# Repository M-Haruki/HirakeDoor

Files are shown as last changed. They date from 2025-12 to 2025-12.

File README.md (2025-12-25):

# ひらけドア (HirakeDoor)

教室ドアの自動化プロジェクト  
[PV映像(YouTube)](https://youtu.be/fkIhEhKD6Qc)

## 概要

教室にある横開きの扉を、センサーやモーターなどを用いて、自動ドア化するプロジェクト。  
距離センサーで人の接近を検知し、ステッピングモーターで扉を開閉する。  
閉じる際はおもりによる重力を利用することで、挟まれ事故などを防止している。  
Webインターフェースを用いて、BluetoothLowEnergy(BLE)経由で、手動による扉の開閉を行うこともできる。(BLEに対応するブラウザが必要)

### 背景

冬の教室で扉すぐ横の席は、扉を開きっぱなしにされると非常に寒い。  
だからといって毎回自分で閉めたり、閉めるようお願いするのも手間がかかる。  
そこでこのプロジェクトが始まった。  
第一段階として、扉におもりを取り付け、開けたら勝手に閉まるようなドアクローザー機構を作成。  
概ね好評だったものの、開けるのが重くなるなどの問題もあり、第二段階としてセンサーやモーターなどを用いた自動ドア化を行った。

### 安全対策

扉を閉じる力はおもりの重力のみを使うことで、挟まれた際のリスクを低減し、扉を手動でも開けられるようにした。

## ギャラリー

||||
|:--:|:--:|:--:|
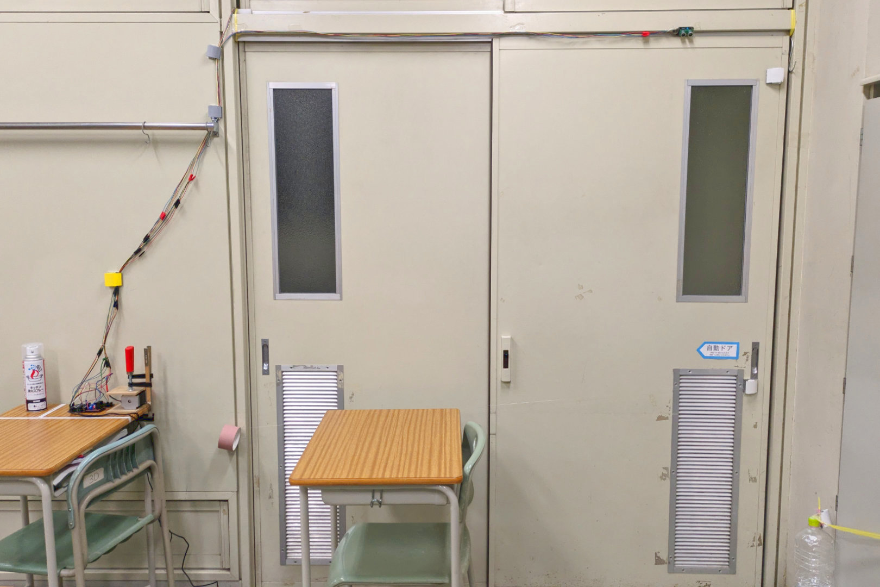
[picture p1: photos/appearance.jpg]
appearance
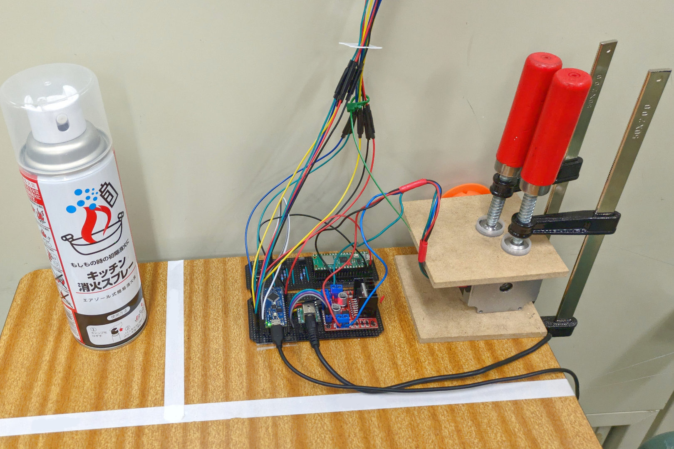
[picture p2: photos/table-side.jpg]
table-side
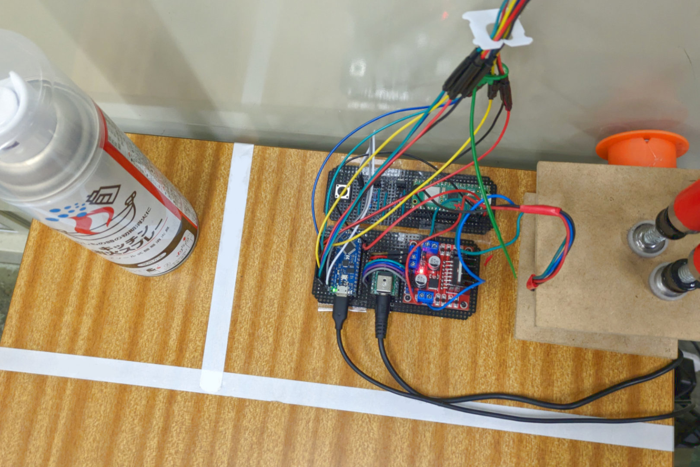
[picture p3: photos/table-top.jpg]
table-top
||||
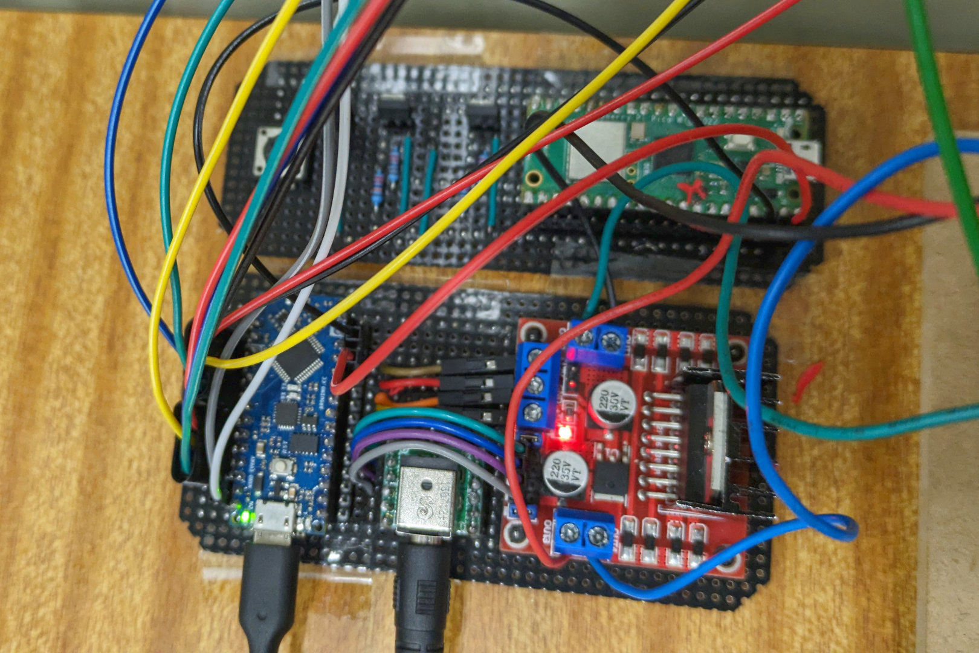
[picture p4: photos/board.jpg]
board
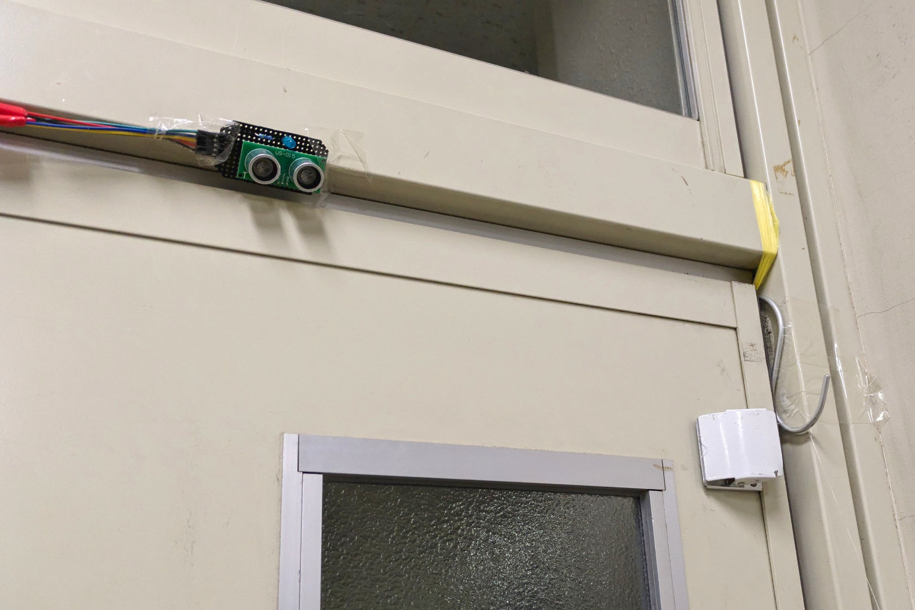
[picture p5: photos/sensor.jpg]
sensor
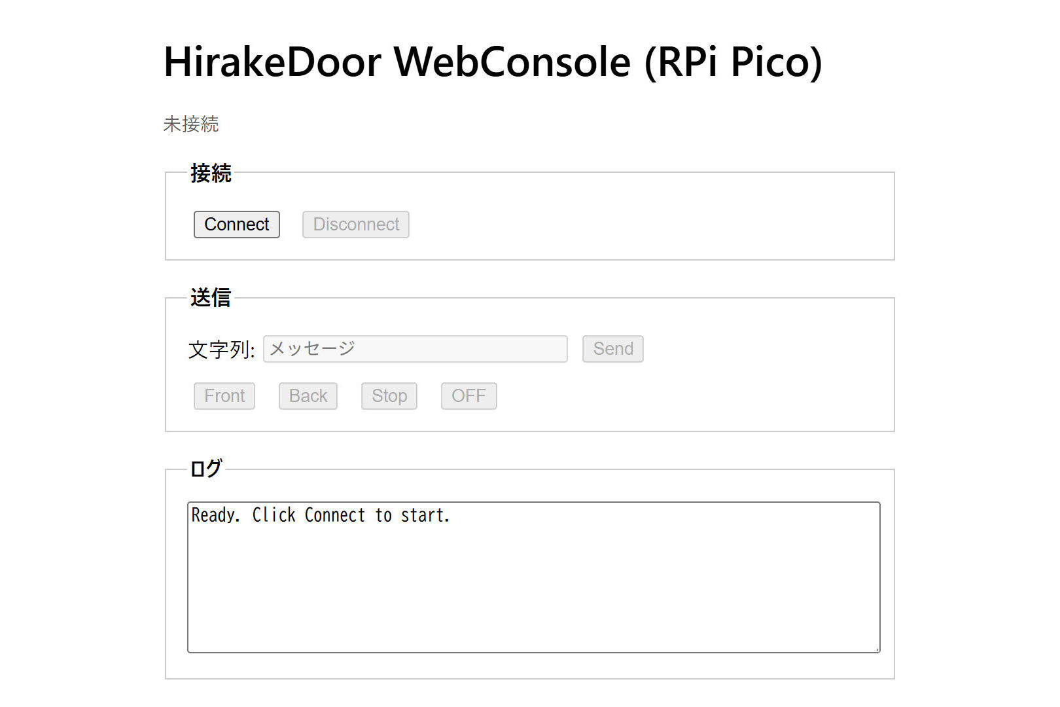
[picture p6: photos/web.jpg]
web
||||

## ソフトウェア構成

- [C++ (Arduino Nano Every)](software/arduino/hirake_door.ino)
- [MicroPython (Raspberry Pi Pico)](software/RPiPico/main.py)
- [HTML (Webインターフェース)](software/web/HirakeDoor.html)

## ハードウェア構成

### 概略図

概略図

### 主要パーツ

- マイコン
  - Arduino Nano Every
  - Raspberry Pi Pico
- ステッピングモーター
  - ST-57BYG076
- モータードライバー
  - L298N モジュール
- 超音波距離センサー
  - US-015

詳細は[hardware/parts.csv](hardware/parts.csv)を参照。

### 回路図

回路図

## クレジット

### プロジェクトメンバー

- M_Haruki
- bearkou
- mochi_kumo
- Mr.Chi

### Special Thanks

- 3D(78th)

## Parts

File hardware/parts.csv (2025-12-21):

Reference | Qty | Value
A1 | 1 | Arduino_Nano_Every
A2 | 1 | RaspberryPi_Pico_W
D1,D2 | 2 | LED
J1 | 1 | Jack-DC
M1 | 1 | ST-57BYG076
Q1,Q2 | 2 | 2SK4017
R1,R2 | 2 | 470Ω
R3,R5 | 2 | 220kΩ
R4,R6 | 2 | 2.2kΩ
SW1 | 1 | SW_Push
U1,U2 | 2 | US-015
U3 | 1 | L298N_Module

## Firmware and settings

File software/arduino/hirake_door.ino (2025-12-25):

// ## 設定構造体とクラス定義
struct SteppingMotorConf
{
  int pinA1;
  int pinA2;
  int pinB1;
  int pinB2;
  float doorPositionLimit;
  float frontStep;
  float backStep;
};

class SteppingMotor
{
private:
  int count = 3; // 0~3
  int pinA1;
  int pinA2;
  int pinB1;
  int pinB2;
  float doorPosition = 0;
  float doorPositionLimit;
  float frontStep;
  float backStep;

  void io(int pin1, int pin2, int state)
  {
    switch (state)
    {
    case -1:
      digitalWrite(pin1, LOW);
      digitalWrite(pin2, HIGH);
      break;
    case 1:
      digitalWrite(pin1, HIGH);
      digitalWrite(pin2, LOW);
      break;
    default:
      digitalWrite(pin1, LOW);
      digitalWrite(pin2, LOW);
      break;
    }
  }

  void move(int a, int b)
  { // -1 or 0 or 1
    io(pinA1, pinA2, a);
    io(pinB1, pinB2, b);
  }

public:
  enum Direction
  {
    Front,
    Back,
  };

  SteppingMotor(const SteppingMotorConf &conf)
  {
    pinA1 = conf.pinA1;
    pinA2 = conf.pinA2;
    pinB1 = conf.pinB1;
    pinB2 = conf.pinB2;
    pinMode(pinA1, OUTPUT);
    pinMode(pinA2, OUTPUT);
    pinMode(pinB1, OUTPUT);
    pinMode(pinB2, OUTPUT);
    doorPositionLimit = conf.doorPositionLimit;
    frontStep = conf.frontStep;
    backStep = conf.backStep;
  }

  bool stepWithLimit(SteppingMotor::Direction direction) // スコープ指定がないとコンパイルエラーになる
  {
    // 超過した値を修正
    if (doorPosition > doorPositionLimit)
    {
      doorPosition = doorPositionLimit;
    }
    else if (doorPosition < 0)
    {
      doorPosition = 0;
    }
    // モーター動作と位置を加算
    if (direction == Front && doorPosition < doorPositionLimit)
    {
      step(Front);
      doorPosition += frontStep;
      if (doorPosition >= doorPositionLimit)
      {
        softStop();
        return true;
      }
      else
      {
        return false;
      }
    }
    else if (direction == Back && doorPosition > 0)
    {
      step(Back);
      doorPosition += backStep;
      if (doorPosition <= 0)
      {
        softStop();
        return true;
      }
      else
      {
        return false;
      }
    }
    else
    {
      return false;
    }
  }

  void step(SteppingMotor::Direction direction)
  {
    // count
    if (direction == Front)
    {
      count += 1;
    }
    else
    {
      count -= 1;
    }
    if (count == 4)
    {
      count = 0;
    }
    else if (count == -1)
    {
      count = 3;
    }
    // move
    switch (count)
    {
    case 0:
      move(1, 1);
      break;
    case 1:
      move(1, -1);
      break;
    case 2:
      move(-1, -1);
      break;
    case 3:
      move(-1, 1);
      break;
    }
  }

  void hardStop()
  {
    switch (count)
    {
    case 0:
      move(1, 1);
      break;
    case 1:
      move(1, -1);
      break;
    case 2:
      move(-1, -1);
      break;
    case 3:
      move(-1, 1);
      break;
    }
  }

  void softStop()
  {
    move(0, 0);
  }

  void resetDoorPosition()
  {
    doorPosition = 0;
  }
};

struct DistanceSensorConf
{
  int pinTrig;
  int pinEcho;
  int pinLed;
  int sampleTimes;
  float sampleTolerance;
  unsigned long ledOnDuration_us;
};

class DistanceSensor
{
private:
  int pinTrig;
  int pinEcho;
  int pinLed;

  int triggerCount = 0; // 0,1,2
  unsigned long triggerTime_us = 0;

  unsigned long startTime;
  unsigned long endTime;
  int lastEchoState;

  static const int sampleTimesMax = 20;
  int sampleTimes;
  int sampleCount;
  float samples[sampleTimesMax];
  float result;
  float sampleTolerance; // 外れ値判定用の許容範囲(中央値に対する割合)

  unsigned long ledOnDuration_us; // LED点灯時間(μs)
  unsigned long ledOnTime_us = 0; // LED点灯時間管理用

  enum SensorMode
  {
    WaitStart,
    Trigger,
    Measuring,
    WaitNextMeasure,
    Completed,
  };
  SensorMode sensorMode = WaitStart;

  void startMeasure()
  {
    lastEchoState = LOW;
    triggerCount = 0; // 安全のため
    sensorMode = Trigger;
  }

  void trigger()
  {
    switch (triggerCount)
    {
    case 0:
      digitalWrite(pinTrig, LOW);
      triggerTime_us = micros();
      triggerCount = 1;
      break;
    case 1:
      if (micros() - triggerTime_us >= 2)
      {
        digitalWrite(pinTrig, HIGH);
        triggerTime_us = micros();
        triggerCount = 2;
      }
      break;
    case 2:
      if (micros() - triggerTime_us >= 10)
      {
        digitalWrite(pinTrig, LOW);
        triggerCount = 0;
        sensorMode = Measuring;
      }
    }
  }

  bool captureEcho()
  {
    // 計測完了でtrueを返す
    int state = digitalRead(pinEcho);
    if (lastEchoState == LOW && state == HIGH)
    {
      // LOW → HIGH（立ち上がり）
      startTime = micros();
      lastEchoState = HIGH;
      return false;
    }
    else if (lastEchoState == HIGH && state == LOW)
    {
      // HIGH → LOW（立ち下がり）
      endTime = micros();
      lastEchoState = LOW;
      return true;
    }
    else
    {
      return false;
    }
  }

  float getDistance()
  {
    long duration = endTime - startTime;
    float distance = duration * 0.0343 / 2.0;
    if (distance >= 2 && distance <= 400)
    {
      return distance;
    }
    else
    {
      return -1;
    }
  }

  float filter()
  {
    // 配列のコピーを作ってソート
    float sorted[sampleTimesMax];
    memcpy(sorted, samples, sampleTimes * sizeof(float));
    for (int i = 0; i < sampleTimes - 1; i++)
    {
      for (int j = i + 1; j < sampleTimes; j++)
      {
        if (sorted[i] > sorted[j])
        {
          float tmp = sorted[i];
          sorted[i] = sorted[j];
          sorted[j] = tmp;
        }
      }
    }
    // 中央値
    float median = sorted[sampleTimes / 2];
    // 外れ値除外(中央値 ± 15%)
    float sum = 0;
    int count = 0;
    for (size_t i = 0; i < sampleTimes; i++)
    {
      if (fabs(samples[i] - median) < median * sampleTolerance)
      {
        sum += samples[i];
        count++;
      }
    }
    // 平均値計算
    if (count == 0)
    {
      return -1; // 全て外れ値 → 失敗
    }
    return sum / count;
  }

public:
  DistanceSensor(const DistanceSensorConf &conf)
  {
    pinTrig = conf.pinTrig;
    pinEcho = conf.pinEcho;
    pinLed = conf.pinLed;
    pinMode(pinTrig, OUTPUT);
    pinMode(pinEcho, INPUT);
    pinMode(pinLed, OUTPUT);
    sampleTimes = conf.sampleTimes;
    sampleTolerance = conf.sampleTolerance;
    ledOnDuration_us = conf.ledOnDuration_us;
  }

  void ledOn()
  {
    digitalWrite(pinLed, HIGH);
    ledOnTime_us = micros();
  }

  void clock()
  {
    switch (sensorMode)
    {
    case Trigger:
      trigger();
      break;
    case Measuring:
      bool isEnd = captureEcho();
      if (isEnd)
      {
        samples[sampleCount] = getDistance();
        sensorMode = WaitNextMeasure;
        sampleCount += 1;
        if (sampleCount == sampleTimes)
        {
          // 平均を計算
          result = filter();
          sensorMode = Completed;
        }
        else
        {
          startMeasure();
        }
      }
      break;
    }
    // LED消灯管理
    if (ledOnTime_us != 0 && micros() - ledOnTime_us >= ledOnDuration_us)
    {
      digitalWrite(pinLed, LOW);
      ledOnTime_us = 0;
    }
  }

  void start()
  {
    if (sensorMode == WaitStart)
    {
      sampleCount = 0;
      startMeasure();
    }
  }

  float getResult()
  {
    if (sensorMode == Completed)
    {
      sensorMode = WaitStart;
      return result;
    }
    else
    {
      return -1;
    }
  }
};

struct ManualControlConf
{
  int pinA;
  int pinB;
};
class ManualControl
{
  // プルアップを介すため、LOWがON、HIGHがOFFになる
private:
  int pinA;
  int pinB;

public:
  enum Status
  {
    Front,
    Back,
    Stop,
  };

  ManualControl(const ManualControlConf &conf)
  {
    pinA = conf.pinA;
    pinB = conf.pinB;
    pinMode(pinA, INPUT_PULLUP);
    pinMode(pinB, INPUT_PULLUP);
  }

  bool isManualMode()
  {
    int stateA = digitalRead(pinA);
    int stateB = digitalRead(pinB);
    if (stateA == HIGH && stateB == HIGH)
    {
      return false;
    }
    else
    {
      return true;
    }
  }

  ManualControl::Status status()
  {
    int stateA = digitalRead(pinA);
    int stateB = digitalRead(pinB);
    if (stateA == LOW && stateB == LOW)
    {
      return ManualControl::Stop;
    }
    else if (stateA == LOW && stateB == HIGH)
    {
      return ManualControl::Front;
    }
    else if (stateA == HIGH && stateB == LOW)
    {
      return ManualControl::Back;
    }
  }
};

// ## enum,プロトタイプ宣言(ないとコンパイルエラーになる)
enum MainMode
{
  Close,
  Opening,
  Open,
  Closing,
  Manual,
};
void changeMode(MainMode newMode);

// ## 変数定義(ユーザー変更可能エリア)
SteppingMotorConf motorConf = {
    .pinA1 = 17,
    .pinA2 = 14,
    .pinB1 = 15,
    .pinB2 = 16,
    .doorPositionLimit = 1450, // ドア全開位置の1/4ステップ数
    .frontStep = 1,
    .backStep = -1,
};
DistanceSensorConf distanceAConf = {
    .pinTrig = 2,
    .pinEcho = 3,
    .pinLed = 4,
    .sampleTimes = 10,           // 1度の距離算出のためのセンサー測定回数
    .sampleTolerance = 0.10,     // 外れ値判定用の許容範囲(中央値に対する割合)
    .ledOnDuration_us = 1000000, // LED点灯時間(μs)
};
DistanceSensorConf distanceBConf = {
    .pinTrig = 8,
    .pinEcho = 9,
    .pinLed = 10,
    .sampleTimes = 10,           // 1度の距離算出のためのセンサー測定回数
    .sampleTolerance = 0.10,     // 外れ値判定用の許容範囲(中央値に対する割合)
    .ledOnDuration_us = 1000000, // LED点灯時間(μs)
};
ManualControlConf manualConf = {
    .pinA = 11,
    .pinB = 12,
};
constexpr unsigned long sensorMeasureInterval_us = 50000;       // センサー測定間隔(μs) 小さすぎると測定に失敗しやすい
constexpr unsigned int detectDistanceMin_cm = 5;                // センサー検出距離下限(cm)
constexpr unsigned int detectDistanceMax_cm = 55;               // センサー検出距離上限(cm)
constexpr unsigned long motorStepDurationFront_us = 3750;       // 開く時のモーター1/4ステップ間隔(μs)
constexpr unsigned long motorStepDurationBack_us = 2650;        // 閉じる時のモーター1/4ステップ間隔(μs)
constexpr unsigned long motorStepDurationMaintenance_us = 7000; // メンテナンス時のモーター1/4ステップ間隔(μs)
constexpr unsigned long openCountLimit_ms = 1000;               // ドア全開時間(ms)
bool enableManualMode = true;                                   // マニュアル制御モード有効フラグ

// ## インスタンス生成,グローバル変数定義
SteppingMotor motor(motorConf);
DistanceSensor distanceA(distanceAConf);
DistanceSensor distanceB(distanceBConf);
ManualControl manual(manualConf);
unsigned long lastTrigTime_us = 0;
unsigned long lastStepTime_us = 0;
unsigned long openCount = 0;
MainMode mode = Close;
int usingSensor = 0; // 0:A, 1:B

// ## 関数定義
void changeMode(MainMode newMode)

{
  switch (newMode)
  {
  case Open:
    openCount = openCountLimit_ms;
    break;
  }
  mode = newMode;
  switch (mode)
  {
  case Opening:
    Serial.println("mode:Opening");
    break;
  case Open:
    Serial.println("mode:Open");
    break;
  case Closing:
    Serial.println("mode:Closing");
    break;
  case Close:
    Serial.println("mode:Close");
    break;
  case Manual:
    Serial.println("mode:Manual");
    break;
  }
}

// ## Arduino標準初期処理
void setup()
{
  Serial.begin(9600);
  delay(1000);
  Serial.println("--Initialized--");
  motor.softStop();
}

// ## Arduino標準ループ処理
void loop()
{

  unsigned long now_us = micros();
  distanceA.clock();
  distanceB.clock();
  // 距離センサーによる検出処理
  if (mode == Close || mode == Closing || mode == Open)
  {
    // センサー起動
    if (now_us - lastTrigTime_us >= sensorMeasureInterval_us)
    {
      lastTrigTime_us = now_us;
      switch (usingSensor)
      {
      case 0:
        usingSensor = 1;
        distanceA.start();
        break;
      case 1:
        usingSensor = 0;
        distanceB.start();
        break;
      }
    }
    // 結果取得
    float resultA = distanceA.getResult();
    float resultB = distanceB.getResult();
    float result = (resultA >= 0) ? resultA : resultB;
    // 検出判定
    if (result >= detectDistanceMin_cm && result <= detectDistanceMax_cm)
    {
      if (resultA >= 0)
      {
        distanceA.ledOn();
      }
      else
      {
        distanceB.ledOn();
      }
      Serial.println("distanceDetect:" + String(result));
      if (mode != Open)
      {
        // temp
        if (mode == Closing)
        {
          Serial.println("temp");
          motor.hardStop();
          delay(1200);
          // delayMicroseconds(500000);
        }
        //
        changeMode(Opening);
      }
      else
      {
        openCount = openCountLimit_ms; // open時に時間延長
      }
    }
  }
  // モーター動作
  switch (mode)
  {
  case Opening:
    if (now_us - lastStepTime_us >= motorStepDurationFront_us)
    {
      // 実行頻度が高いため、ここにSerial.println()を入れると距離センサー系の機能がうまく動かない
      lastStepTime_us = now_us;
      bool isEnd = motor.stepWithLimit(SteppingMotor::Front);
      if (isEnd)
      {
        changeMode(Open);
      }
    }
    break;
  case Closing:
    if (now_us - lastStepTime_us >= motorStepDurationBack_us)
    {
      lastStepTime_us = now_us;
      bool isEnd = motor.stepWithLimit(SteppingMotor::Back);
      if (isEnd)
      {
        changeMode(Close);
      }
    }
    break;
  case Open:
    if (now_us - lastStepTime_us >= 1000 && openCount > 0) // 1msごとにトリガー
    {
      lastStepTime_us = now_us;
      openCount -= 1;
      motor.hardStop();
      if (openCount == 0)
      {
        changeMode(Closing);
      }
    }
    break;
  case Manual:
    ManualControl::Status status = manual.status();
    switch (status)
    {
    case ManualControl::Front:
      if (now_us - lastStepTime_us >= motorStepDurationMaintenance_us)
      {
        lastStepTime_us = now_us;
        motor.step(SteppingMotor::Front);
      }
      break;
    case ManualControl::Back:
      if (now_us - lastStepTime_us >= motorStepDurationMaintenance_us)
      {
        lastStepTime_us = now_us;
        motor.step(SteppingMotor::Back);
      }
      break;
    case ManualControl::Stop:
      motor.softStop();
      break;
    }
    break;
  }
  // マニュアル制御確認
  if (enableManualMode)
  {
    if (manual.isManualMode() && mode != Manual)
    {
      changeMode(Manual);
    }
    else if (!manual.isManualMode() && mode == Manual)
    {
      motor.resetDoorPosition();
      changeMode(Close);
    }
  }
}

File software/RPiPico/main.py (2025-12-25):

# BleTest.py
# https://logikara.blog/picow-ble-micropython を参照して作成
# BLEのPeripheralとして振る舞う

import aioble  # MicroPythonのBLEライブラリ
import bluetooth  # MicroPythonのBLEモジュール
import uasyncio as asyncio  # 非同期処理ライブラリ
from machine import Pin  # PicoのGPIOモジュールをインポート

UART_SERVICE_UUID = bluetooth.UUID(
    "6E400001-B5A3-F393-E0A9-E50E24DCCA9E"
)  # UARTサービスUUID
UART_RX_CHAR_UUID = bluetooth.UUID(
    "6E400002-B5A3-F393-E0A9-E50E24DCCA9E"
)  # UART受信用キャラクタリスティックUUID
UART_TX_CHAR_UUID = bluetooth.UUID(
    "6E400003-B5A3-F393-E0A9-E50E24DCCA9E"
)  # UART送信用キャラクタリスティックUUID

# サービスとキャラクタリスティックの定義
uart_service = aioble.Service(UART_SERVICE_UUID)  # UARTサービスを定義
tx_char = aioble.Characteristic(
    uart_service, UART_TX_CHAR_UUID, read=True, notify=True
)  # UART送信用キャラクタリスティックを定義
rx_char = aioble.Characteristic(
    uart_service, UART_RX_CHAR_UUID, write=True, write_no_response=True, capture=True
)  # UART受信用キャラクタリスティックを定義

aioble.register_services(uart_service)  # GATTサービスを登録

led = Pin("LED", Pin.OUT)  # LED端子をledとして出力に設定
out_a = Pin(16, Pin.OUT)
out_b = Pin(17, Pin.OUT)
out_a.value(0)  # 初期状態はOFF
out_b.value(0)
# sw_main = Pin(14, Pin.IN, Pin.PULL_DOWN)  # 送信ボタン
sw_reset = Pin(15, Pin.IN, Pin.PULL_DOWN)  # 接続解除用ボタン


# 非同期でタスクを実行
async def handle_rx(connection):
    # 受信待ちループ
    while connection.is_connected():
        try:
            _, value = await rx_char.written()  # 戻り値のconnectionは未使用
            print("Received:", value)
            v = value.strip().lower()
            if v == b"front":
                out_a.value(1)
                out_b.value(0)
            elif v == b"back":
                out_a.value(0)
                out_b.value(1)
            elif v == b"stop":
                out_a.value(1)
                out_b.value(1)
            elif v == b"off":
                out_a.value(0)
                out_b.value(0)
        except asyncio.CancelledError:
            raise
        except Exception as e:
            print("ReceiveError:", e)
            break


# async def handle_tx(connection):
#     # 送信ループ（変化時のみ通知）
#     last = None
#     while connection.is_connected():
#         try:
#             value = "on" if sw_main.value() else "off"
#             if value != last:
#                 last = value
#                 try:
#                     await tx_char.notify(connection, value.encode())
#                 except asyncio.CancelledError:
#                     raise
#                 except Exception:
#                     # 未購読や一時的な送信失敗はスキップ
#                     pass
#         except asyncio.CancelledError:
#             raise
#         except Exception as e:
#             print("SendError:", e)
#             break
#         await asyncio.sleep_ms(100)


async def handle_disconnect(connection):
    # 接続解除ボタン用ループ
    while connection.is_connected():
        try:
            if sw_reset.value():
                await connection.disconnect()
        except asyncio.CancelledError:
            raise
        except Exception as e:
            print("DisconnectError:", e)
            break
        await asyncio.sleep_ms(100)


# BLE Peripheralとして動作するメインループ
async def ble_peripheral_loop():
    led.value(1)
    await asyncio.sleep_ms(3000)  # 起動後3秒間LED点灯
    led.value(0)
    while True:
        led.value(0)  # 接続待機中はLED消灯
        print("Waiting connect...")
        try:
            async with await aioble.advertise(  # BLEアドバタイズを開始
                250_000,  # アドバタイズ間隔（マイクロ秒）
                name="HirakeDoor_RPiPico",  # アドバタイズ名（BLE接続デバイス名）
                services=[UART_SERVICE_UUID],  # サービスUUIDを指定
            ) as connection:  # 接続待機
                print("Connecting:", connection.device)  # 接続されたデバイス情報を表示
                led.value(1)

                # 受信処理を別タスクで開始
                rx_task = asyncio.create_task(handle_rx(connection))
                # tx_task = asyncio.create_task(handle_tx(connection))
                disconnect_task = asyncio.create_task(handle_disconnect(connection))

                # 接続が切れるまで待機
                while connection.is_connected():
                    await asyncio.sleep_ms(100)

                # 接続解除 → タスクキャンセル
                rx_task.cancel()
                # tx_task.cancel()
                disconnect_task.cancel()
                led.value(0)  # LED消灯
                print("Disconnected")

        except Exception as e:
            print("Advertise:", repr(e))

        await asyncio.sleep_ms(200)


# 実行
try:
    # PicoのBLE Peripheralとして動作開始
    asyncio.run(ble_peripheral_loop())
except KeyboardInterrupt:
    led.value(0)
    out_a.value(0)
    out_b.value(0)
    print("Cleanup done.")

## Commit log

2025-12-14 関連ファイル追加
    [fritzing.fzz]
2025-12-14 SteppingMotorおよびDistanceSensorクラスのプライベートメソッドを整理し、公開メソッドを追加
2025-12-14 マニュアルモードを実装
2025-12-14 回路画像を追加
2025-12-15 センサー2台体制
2025-12-15 測定結果統合ロジック効率化
2025-12-15 初期値更新
2025-12-15 回路データを更新
    [fritzing.fzz]
2025-12-15 回路データを更新(未エクスポート)
    [fritzing.fzz]
2025-12-16 距離センサーの外れ値判定用の許容範囲を追加
2025-12-17 モーター制御ロジックの修正と手動モードの有効化
2025-12-17 回路図を更新
    [fritzing.fzz]
2025-12-18 ステッピングモーターと距離センサーの設定を改善し、LED制御機能を追加
2025-12-18 freeStop()の実行をMotorクラス側に持たせる
2025-12-18 モーター停止メソッドの名称を変更し、コードの可読性を向上させる
2025-12-18 距離センサーのLED制御機能を追加し、changeMode関数の引数を簡素化
2025-12-18 ManualControlの停止メソッドをsoftStopに変更し、モード遷移の処理を改善
2025-12-18 LED制御の初期状態を設定し、BLE周辺機器ループ内での出力ポートの状態をリセット
2025-12-19 ドア位置リセットメソッドを追加し、距離センサーのLED点灯時間を延長、モーターのステップ間隔を調整
2025-12-19 プロジェクト名を「HirakeDoma」から「HirakeDoor」に変更し、関連するファイルのタイトルを更新
2025-12-19 回路図などを更新
    [fritzing.fzz]
2025-12-19 回路図等の更新
    [fritzing.fzz]
2025-12-21 README.mdのプロジェクト概要と動機を明確にするために、説明文を追加・修正
2025-12-21 メタデータの説明文を修正し、デバイス名を「HirakeDoma」から「HirakeDoor」に変更
2025-12-21 ディレクトリ構成を変更
    [fritzing.fzz]
2025-12-21 回路図等を追加
    [parts.csv]
2025-12-21 README.mdの概要と構成概要を整理し、ハードウェアとソフトウェアのセクションを追加
2025-12-21 README.mdの動機セクションを追加し、構成概要を整理
2025-12-21 readmeを更新
2025-12-22 回路図を訂正
2025-12-25 Add overview diagram and update schematic image
    Added a diagram and updated the schematic image.
2025-12-25 コードを反映
2025-12-25 切断時の出力ピンの初期化を削除 (revert 3211201fa11406e91ee6fee655e99b7049aeb903)
2025-12-25 回路図の更新
2025-12-25 README.mdにギャラリーセクションを追加し、関連画像を追加
